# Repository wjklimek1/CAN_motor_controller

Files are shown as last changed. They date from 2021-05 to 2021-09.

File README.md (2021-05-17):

# CAN motor controller
This project is a device that allows control of DC motor by commands on CAN bus. It is based on STM32F103 microcontroller that interprets CAN messages and drives motor using two BTN8982 half-bridges configured as a single H-bridge. 

## Motor driving capabilities
DC motor is controlled with 21kHz PWM signal with 0-100% duty. PWM can be regulated in 0.1% steps - from 0 to 1000. Theoretically max current that MOSFETs can handle is 55A, but it can be futher limited by traces width and connectors. It was tested up to 10A, but should handle much more without any problems. Power supply voltage range is 5-24V.
| Parameter | Min | Max |
|--|--|--|
| voltage | 5V | 24V |
| motor current |  | 55A (10A tested) |

Motor is accelerated slowly by changing PWM duty. If received command orders to immediately set PWM to 100% from 0%, duty is increased slowly in default 10ms intervals. Therefore spinning motor to top speed will take 10s. This property can be disabled by setting "motor inertia" parameter to 0 (see CAN commands table).

## CAN configuration
CAN bus in STM32F103 runs on 250kb/s by default. It can be set to other, hard coded value in the initialization function. Other supported baudrates are 500kb/s and 1Mb/s. 

## Heartbeat
Device emits "heartbeat" frame every 1s. It is an empty frame with ID = 0x444. Heartbeat can be disabled or it's period can be changed in 1s steps up to 255s.

## CAN message structure
Device utilizes two identifiers - 0x444 for commands and 0x445 for requesting data. This values are hard coded too, but can be changed in *canbus.h* file. DLC of CAN messages is not really important, but it cannot be shorter than expected.
In both commands and data requests first byte of message is code of command or data request. In commands next bytes represent values of command parameters. When data request is received by device, it will respond with frame of the same ID and data request code. Next bytes will contain requested data.

## Commands
Following table shows available commands:
|Command | frame ID | DLC | byte 0 (command code) | byte 1 | byte 2 | byte 3 |
|--|--|--|--|--|--|--|
|Set speed | 0x444 | 4 | 1 | rotation direction (0 or 1) | MSB of speed | LSB of speed|
|Set max temperature internal | 0x444 | 2 | 2 | max internal temperature (uint8_t) in Celcius | - | - |
|Set max temperature external | 0x444 | 2 | 3 | max external temperature (uint8_t) in Celcius | - | - |
|Set max current | 0x444 | 4 | 4 | MSB of max current (mA) | LSB of max current (mA) | - |
|Emergency stop | 0x444 | 1 | 5 | - | - | - |
|Set inertia | 0x444 | 2 | 6 | Inertia (ms delay between changing PWM duty) | - | - |
|Set heartbeat | 0x444 | 2 | 7 | heartbeat interval (0 for disabled) | - | - |

## Data requests
To request data, frame of ID = 0x445 and first byte containing data request code can be sent. Device will respond with similar frame, but containing data in next bytes.
 
Following table shows available data requests:
|Data request | frame ID | DLC | byte 0 (data request code) | byte 1 | byte 2 | byte 3 | byte 4 |byte 5 |
|--|--|--|--|--|--|--|--|--|
|Internal temperature | 0x445 | 2 | 1 | Internal temperature (uint8_t) in |Celcius | - | - | - | - |
|External temperature | 0x445 | 2 | 2 | External temperature (uint8_t) in |Celcius | - | - | - | - |
|Power supply voltage | 0x445 | 3 | 3 | MSB of voltage in mV | LSB of voltage in mV | - | - | - |
|Motor current | 0x445 | 3 | 4 | MSB of current in mA | LSB of current in mA | - | - | - |
|Speed | 0x445 | 4 | 5 | rotation direction (0 or 1) | MSB of speed | LSB of speed| - | - |
|Target speed | 0x445 | 4 | 6 | rotation direction (0 or 1) | MSB of speed | LSB of speed| - | - |
|Errors | 0x445 | 5 | 7 | MOSFET fault | overcurrent | overtemperature internal | overtemperature external | emergency stop |

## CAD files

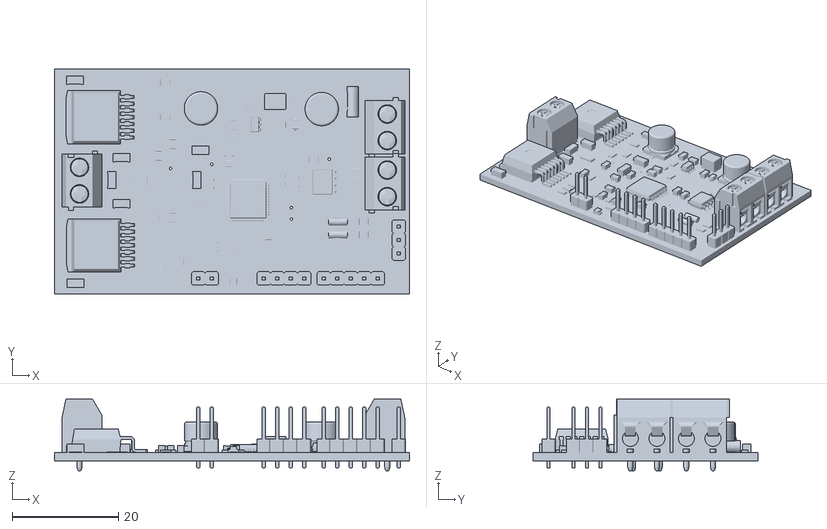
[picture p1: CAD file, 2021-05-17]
PCB_and_schematic/3D_models/CAN_motor_controller.stl
66.8 x 42.4 x 13.5

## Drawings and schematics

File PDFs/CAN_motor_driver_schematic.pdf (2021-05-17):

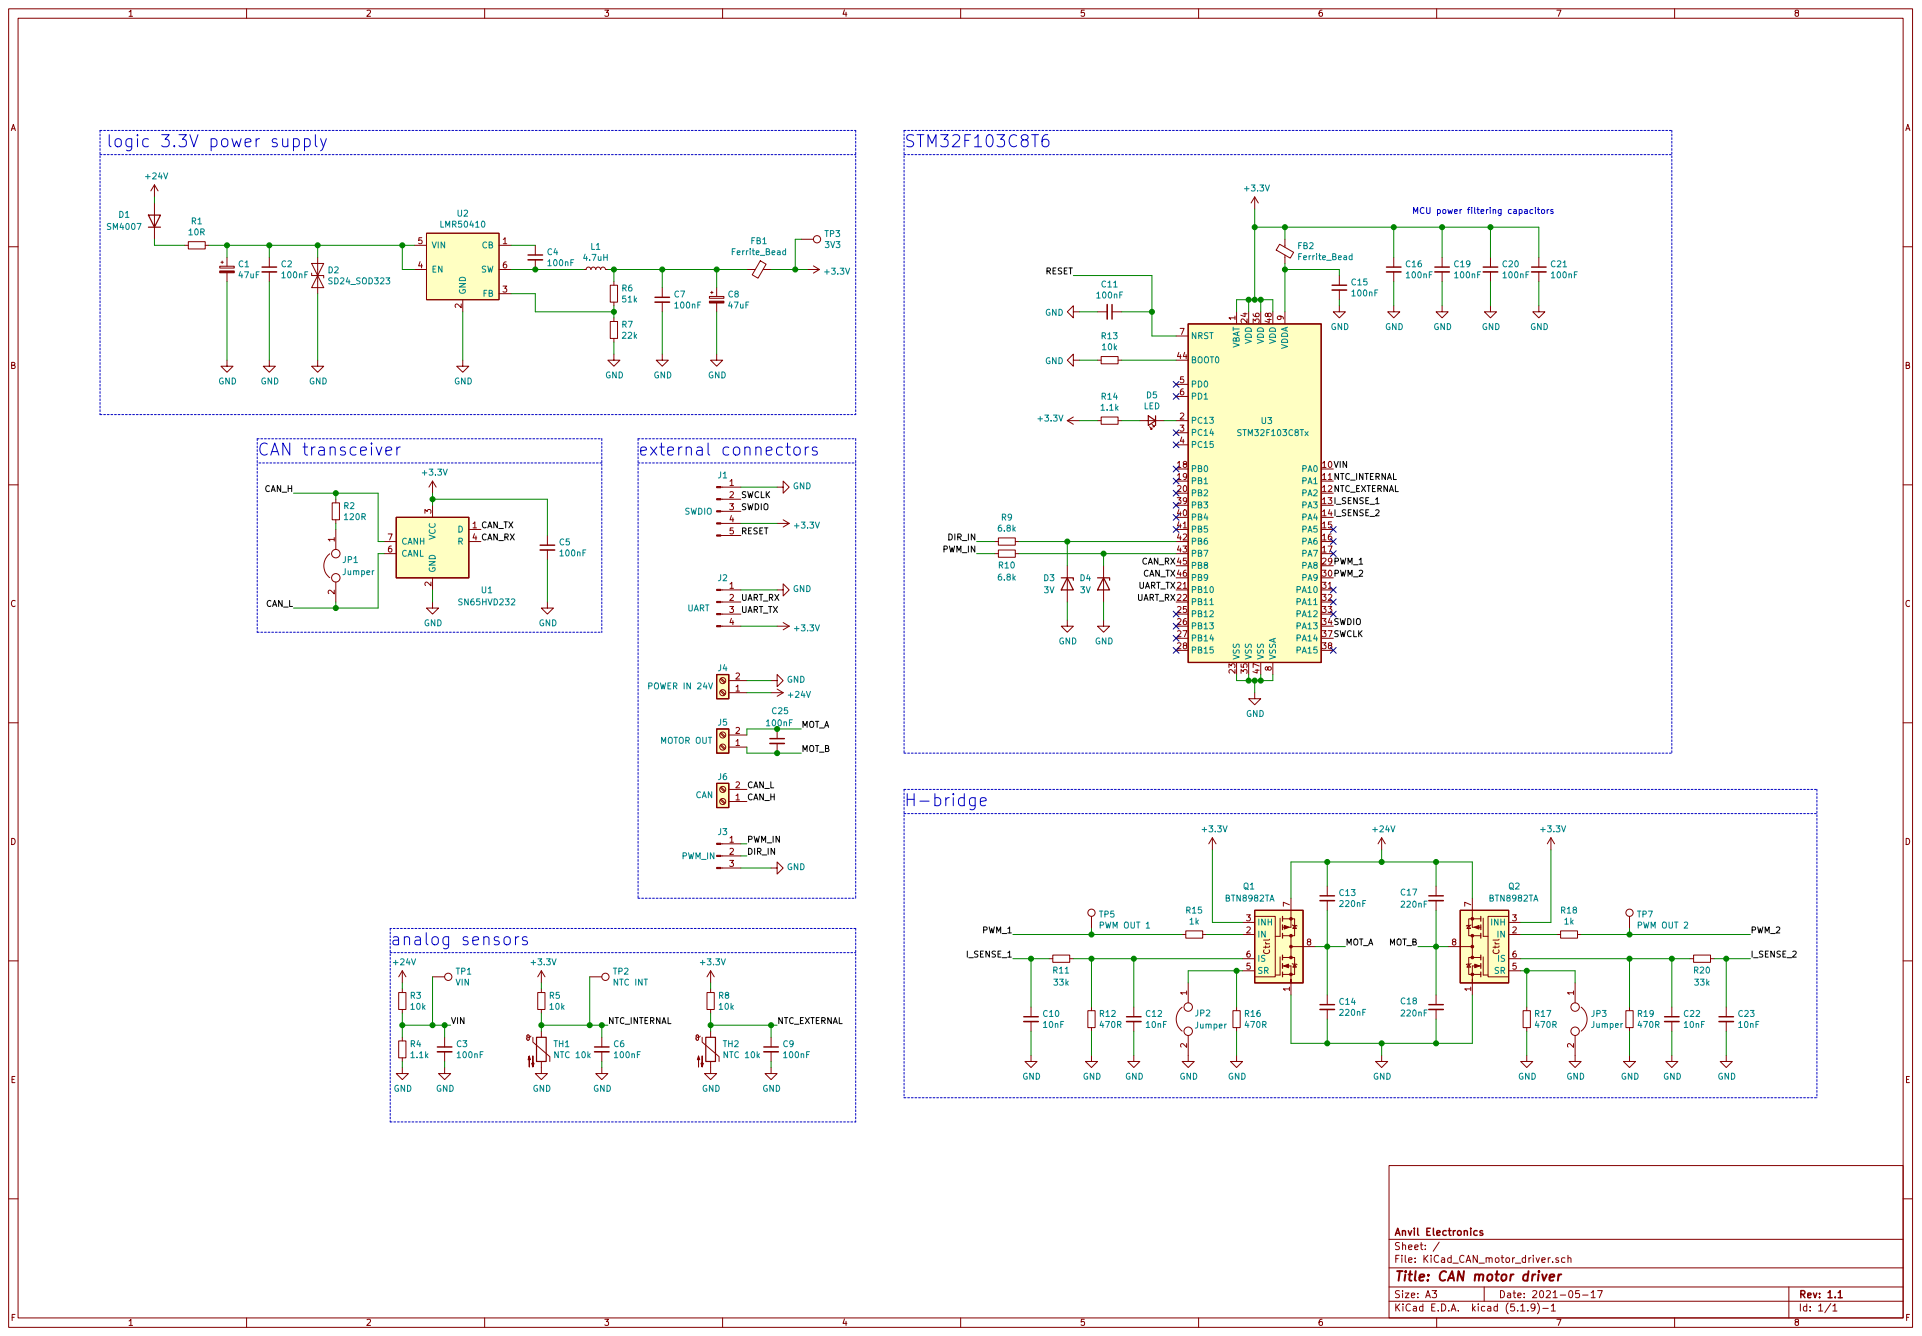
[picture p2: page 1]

2 FB 3 EN 4 VIN 5 SW 6 U2

MCU power filtering capacitors

1 VDD 24 VDD 36 VDD 48 VDDA

9 VSS 23 VSS 35 VSS 47 VSSA

TP7 PWM OUT 2 TP2 NTC INT

File: KiCad_CAN_motor_driver.sch Sheet: / Anvil Electronics

Id: 1/1 Title: CAN motor driver

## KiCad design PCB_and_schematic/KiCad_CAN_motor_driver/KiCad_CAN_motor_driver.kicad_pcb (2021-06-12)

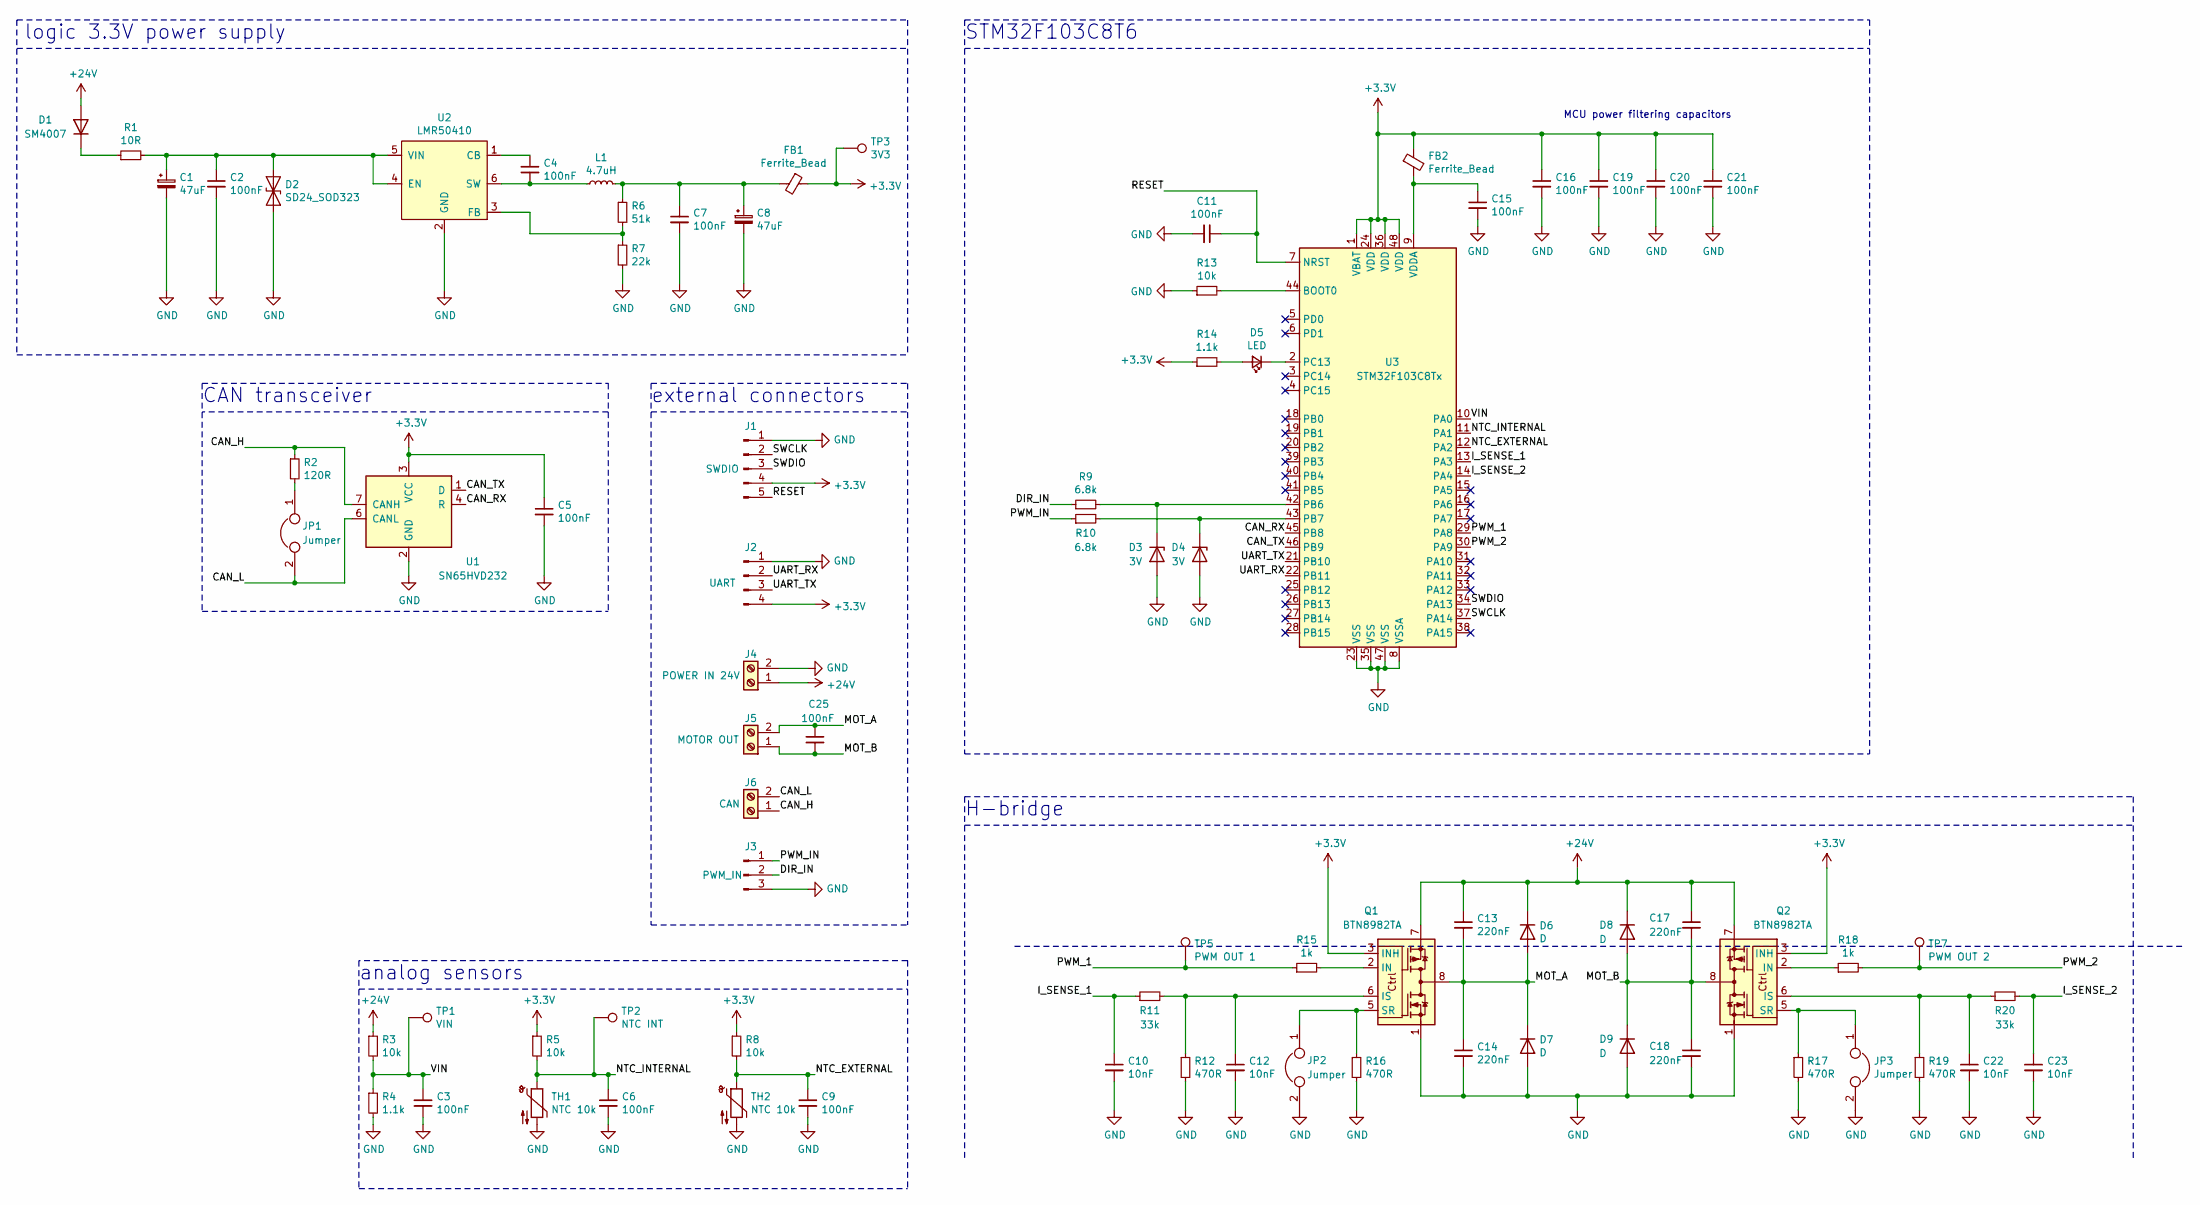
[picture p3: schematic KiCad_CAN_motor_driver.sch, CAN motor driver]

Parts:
C1, C8: 47uF; CP_Elec_6.3x5.7
C2, C3, C4, C5, C6, C7, C9, C11, C15, C16, C19, C20, C21: 100nF; C_0805_2012Metric
C10, C12, C22, C23: 10nF; C_0805_2012Metric
C13, C14, C17, C18: 220nF; C_1206_3216Metric_Pad1.33x1.80mm_HandSolder
C25: 100nF; C_1206_3216Metric
D1: SM4007; D_MELF
D2: SD24_SOD323; D_SOD-323
D3, D4: 3V; D_MiniMELF
D5: LED; LED_0805_2012Metric_Castellated
D6, D7, D8, D9: D; D_PowerDI-123
FB1: Ferrite_Bead; L_1206_3216Metric
FB2: Ferrite_Bead; L_1206_3216Metric_Pad1.22x1.90mm_HandSolder
J1: SWDIO; PinHeader_1x05_P2.54mm_Vertical
J2: UART; PinHeader_1x04_P2.54mm_Vertical
J3: PWM_IN; PinHeader_1x03_P2.54mm_Vertical
J4: POWER IN 24V; ScrewTerminal_2_P5.08mm
J5: MOTOR OUT; ScrewTerminal_2_P5.08mm
J6: CAN; ScrewTerminal_2_P5.08mm
JP1: Jumper; SolderJumper-2_P1.3mm_Open_Pad1.0x1.5mm
JP2, JP3: Jumper; SolderJumper-2_P1.3mm_Bridged_Pad1.0x1.5mm
L1: 4.7uH; L_Wuerth_MAPI-4030
Q1, Q2: BTN8982TA; TO-263-7_TabPin8
R1: 10R; R_0805_2012Metric
R2: 120R; R_0805_2012Metric
R3, R5, R8, R13: 10k; R_0805_2012Metric
R4, R14: 1.1k; R_0805_2012Metric
R6: 51k; R_0805_2012Metric
R7: 22k; R_0805_2012Metric
R9, R10: 6.8k; R_0805_2012Metric
R11, R20: 33k; R_0805_2012Metric
R12, R16, R17, R19: 470R; R_0805_2012Metric
R15, R18: 1k; R_0805_2012Metric
TH1: NTC 10k; R_1206_3216Metric_Pad1.30x1.75mm_HandSolder
TH2: NTC 10k; PinHeader_1x02_P2.54mm_Vertical
TP1: VIN; TestPoint_THTPad_D1.0mm_Drill0.5mm
TP2: NTC INT; TestPoint_THTPad_D1.0mm_Drill0.5mm
TP3: 3V3; TestPoint_THTPad_D1.0mm_Drill0.5mm
TP5: PWM OUT 1; TestPoint_THTPad_D1.0mm_Drill0.5mm
TP7: PWM OUT 2; TestPoint_THTPad_D1.0mm_Drill0.5mm
U1: SN65HVD232; SOIC-8_3.9x4.9mm_P1.27mm
U2: LMR50410; SOT-23-6_Handsoldering
U3: STM32F103C8Tx; LQFP-48_7x7mm_P0.5mm

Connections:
+3V3: C5.1, C16.1, C19.1, C20.1, C21.1, FB1.1, FB2.1, J1.4, J2.4, Q1.3 (INH), Q2.3 (INH), R5.1, R8.1, R14.1, TP3.1, U1.3 (VCC), U3.1 (VBAT), U3.24 (VDD), U3.36 (VDD), U3.48 (VDD)
+24V: C13.1, C17.1, D1.2 (A), D6.1 (K), D8.1 (K), J4.1, Q1.7, Q2.7, R3.1
/CAN_H: J6.1, R2.1, U1.7 (CANH)
/CAN_L: J6.2, JP1.2, U1.6 (CANL)
/CAN_RX: U1.4 (R), U3.45 (PB8)
/CAN_TX: U1.1 (D), U3.46 (PB9)
/DIR_IN: J3.2, R9.1
/I_SENSE_1: C10.1, R11.1, U3.13 (PA3)
/I_SENSE_2: C23.1, R20.2, U3.14 (PA4)
/MOT_A: C13.2, C14.1, C25.1, D6.2 (A), D7.1 (K), J5.2, Q1.4, Q1.8
/MOT_B: C17.2, C18.1, C25.2, D8.2 (A), D9.1 (K), J5.1, Q2.4, Q2.8
/NTC_EXTERNAL: C9.1, R8.2, TH2.1, U3.12 (PA2)
/NTC_INTERNAL: C6.1, R5.2, TH1.1, TP2.1, U3.11 (PA1)
/PWM_1: R15.1, TP5.1, U3.29 (PA8)
/PWM_2: R18.2, TP7.1, U3.30 (PA9)
/PWM_IN: J3.1, R10.1
/RESET: C11.1, J1.5, U3.7 (NRST)
/SWCLK: J1.2, U3.37 (PA14)
/SWDIO: J1.3, U3.34 (PA13)
/UART_RX: J2.2, U3.22 (PB11)
/UART_TX: J2.3, U3.21 (PB10)
/VIN: C3.1, R3.2, R4.1, TP1.1, U3.10 (PA0)
GND: C1.2, C2.2, C3.2, C5.2, C6.2, C7.2, C8.2, C9.2, C10.2, C11.2, C12.2, C14.2, C15.2, C16.2, C18.2, C19.2, C20.2, C21.2, C22.2, C23.2, D2.2 (A2), D3.2 (A), D4.2 (A), D7.2 (A), D9.2 (A), J1.1, J2.1, J3.3, J4.2, JP2.2, JP3.2, Q1.1, Q2.1, R4.2, R7.2, R12.2, R13.1, R16.2, R17.2, R19.2, TH1.2, TH2.2, U1.2 (GND), U2.2 (GND), U3.8 (VSSA), U3.23 (VSS), U3.35 (VSS), U3.47 (VSS)
unnamed: C1.1, C2.1, D2.1 (A1), R1.2, U2.4 (EN), U2.5 (VIN)
unnamed: C4.1, U2.1 (CB)
unnamed: C4.2, L1.1, U2.6 (SW)
unnamed: C7.1, C8.1, FB1.2, L1.2, R6.1
unnamed: C12.1, Q1.6 (IS), R11.2, R12.1
unnamed: C15.1, FB2.2, U3.9 (VDDA)
unnamed: C22.1, Q2.6 (IS), R19.1, R20.1
unnamed: D1.1 (K), R1.1
unnamed: D3.1 (K), R9.2, U3.42 (PB6)
unnamed: D4.1 (K), R10.2, U3.43 (PB7)
unnamed: D5.1 (K), U3.2 (PC13)
unnamed: D5.2 (A), R14.2
unnamed: JP1.1, R2.2
unnamed: JP2.1, Q1.5 (SR), R16.1
unnamed: JP3.1, Q2.5 (SR), R17.1
unnamed: Q1.2 (IN), R15.2
unnamed: Q2.2 (IN), R18.1
unnamed: R6.2, R7.1, U2.3 (FB)
unnamed: R13.2, U3.44 (BOOT0)

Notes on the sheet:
logic 3.3V power supply
MCU power filtering capacitors
external connectors
CAN transceiver
analog sensors
H-bridge
STM32F103C8T6

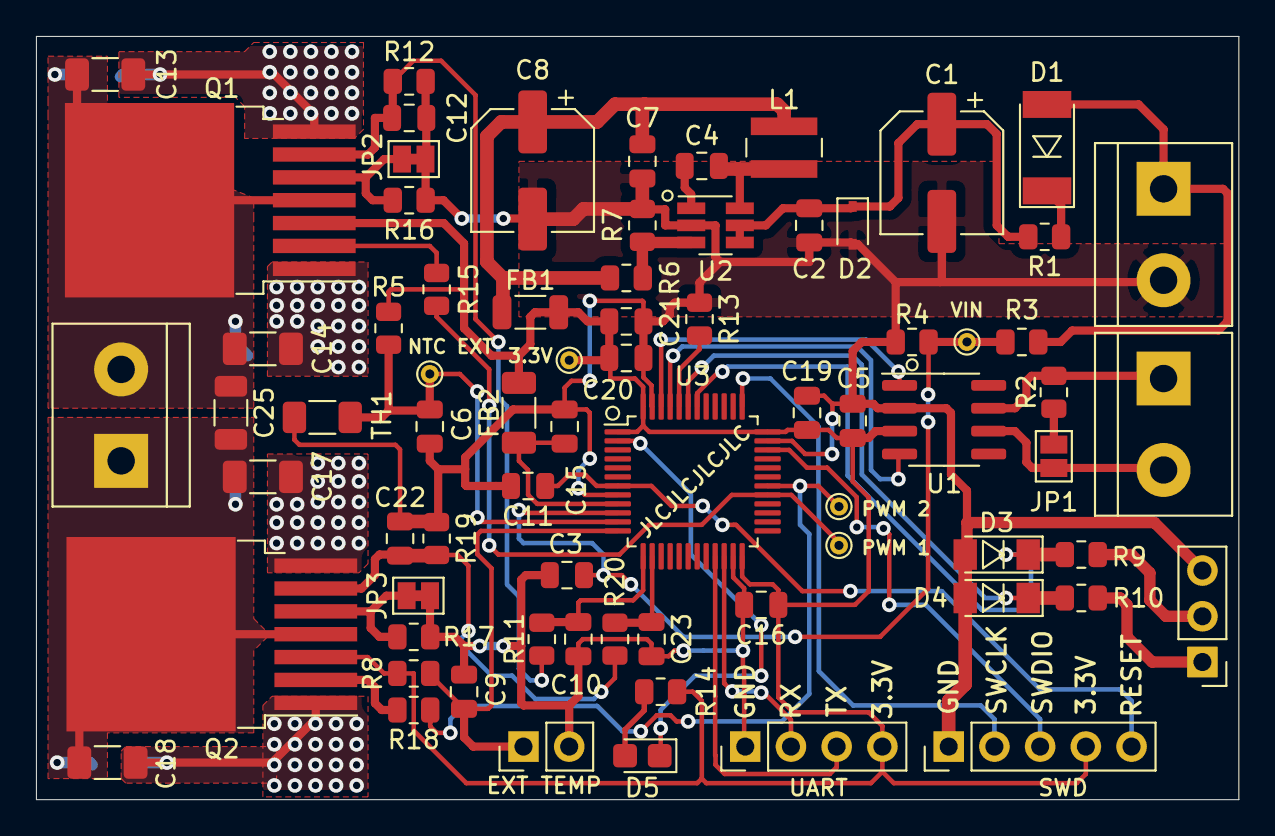
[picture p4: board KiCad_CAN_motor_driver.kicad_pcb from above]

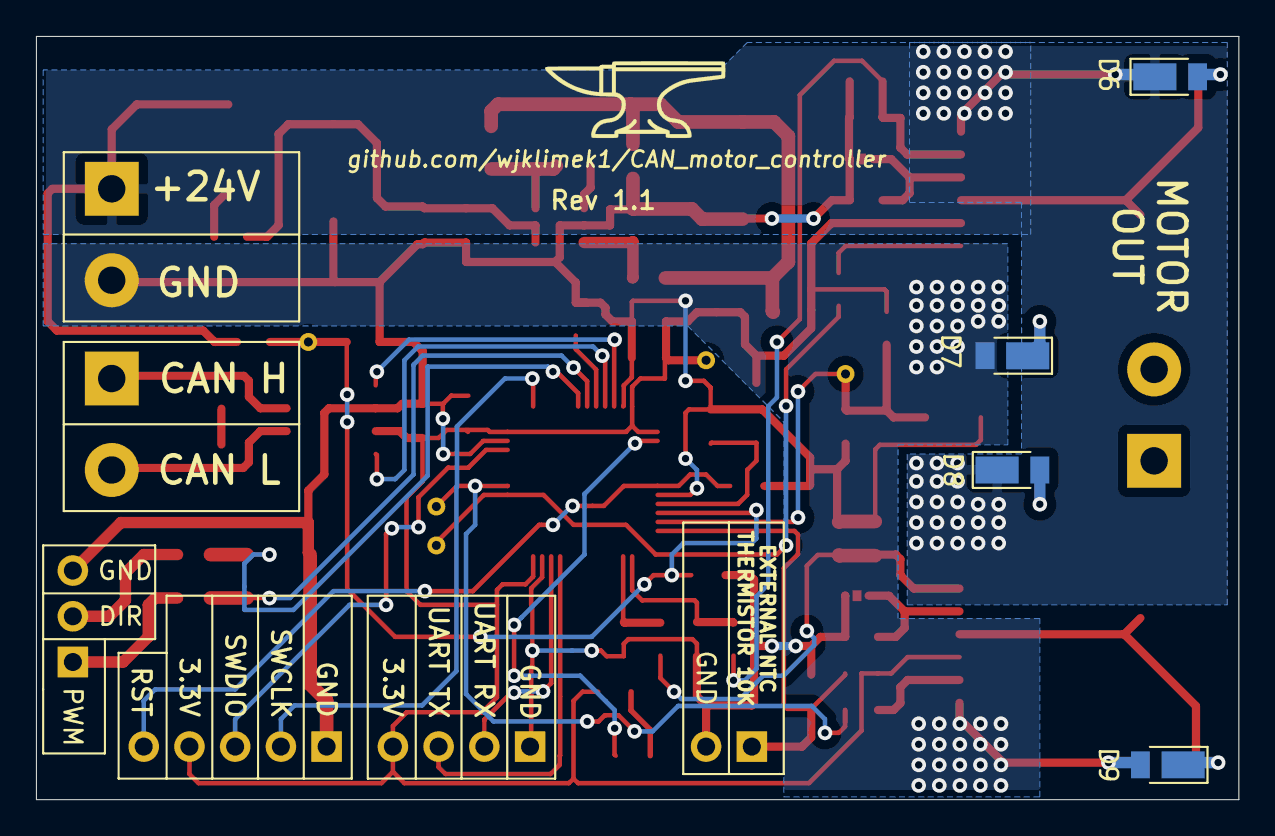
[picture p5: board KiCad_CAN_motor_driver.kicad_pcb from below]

Board: 2 copper layers, 66.8 x 42.4 mm, 77 parts (4 on the bottom side), 42 nets.

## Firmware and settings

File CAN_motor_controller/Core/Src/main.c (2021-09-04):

#include <stdint.h>
#include "stm32f103xb.h"

#include "timers.h"
#include "clock.h"
#include "adc.h"
#include "uart.h"
#include "printf.h"
#include "canbus.h"
#include "ringbuffer.h"
#include "thermistor.h"
#include "command_interpreter.h"

volatile uint16_t ADC_raw_values[6];
volatile CANbus_RX_buffer_t rx_buffer;

int main()
{
  set_system_clock_to_64Mhz();

  SysTick_init(64000);
  TIM1_init_and_start();
  ADC_init();
  ADC_start_with_DMA((uint16_t*)ADC_raw_values);
  UART3_init(64000000, 115200);

  CAN1_init(250000);
  CAN1_config_filter(0, COMMAND_MSG_ID, 0);
  CAN1_config_filter(1, DATARQ_MSG_ID, 1);

  ringbuffer_init(&rx_buffer);

  RCC->APB2ENR |= RCC_APB2ENR_IOPCEN;  //enable gpio port C clock
  GPIOC->CRH &= ~(GPIO_CRH_MODE13_Msk);
  GPIOC->CRH |= (GPIO_CRH_MODE13_1);
  GPIOC->CRH &= ~(GPIO_CRH_CNF13_Msk); //turn on LED

  while(1)
  {
    command_interpreter(&rx_buffer);
    follow_target_speed();
    transmit_heartbeat();
  }
}

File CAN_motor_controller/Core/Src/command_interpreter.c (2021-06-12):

#include <stdint.h>
#include "stm32f103xb.h"

#include "timers.h"
#include "clock.h"
#include "adc.h"
#include "uart.h"
#include "printf.h"
#include "canbus.h"
#include "thermistor.h"
#include "ringbuffer.h"
#include "command_interpreter.h"

extern volatile uint16_t ADC_raw_values[6];
extern volatile CANbus_RX_buffer_t rx_buffer;

uint8_t _heartbeat_interval = 1;
uint8_t _motor_inertia = 10;
uint8_t _emergency_stop = 0;
uint8_t _motor_dir = 0;
uint16_t _motor_speed = 0;
uint8_t _target_motor_dir = 0;
uint16_t _target_motor_speed = 0;

uint8_t _max_current = 30;
uint8_t _max_temperature_int = 90;
uint8_t _max_temperature_ext = 90;

int8_t command_interpreter(volatile CANbus_RX_buffer_t *rx_buffer)
{
  if (ringbuffer_elements_pending(rx_buffer) > 0)
  {
    CANbus_msg_t msg = ringbuffer_get_msg(rx_buffer);

    if (msg.stdID == COMMAND_MSG_ID)
    {
      switch (msg.data[0])
	{
	case SET_SPEED:
	  set_speed(msg);
	  break;
	case SET_MAX_CURR:
	  set_max_curr(msg);
	  break;
	case SET_MAX_TEMP_INTERNAL:
	  set_max_temp_int(msg);
	  break;
	case SET_MAX_TEMP_EXTERNAL:
	  set_max_temp_ext(msg);
	  break;
	case EMERGENCY_STOP:
	  emergency_stop();
	  break;
	case SET_INERTIA:
	  set_motor_inertia(msg);
	  break;
	case SET_HEARTBEAT:
	  set_heartbeat(msg);
	  break;
	default:
	  return UNKNOWN_COMMAND;
	  break;
	}
    }
    else if (msg.stdID == DATARQ_MSG_ID)
    {
      switch (msg.data[0])
	{
	case GET_TEMP_INTERNAL:
	  transmit_temperature_internal();
	  break;
	case GET_TEMP_EXTERNAL:
	  transmit_temperature_external();
	  break;
	case GET_VOLTAGE:
	  transmit_voltage();
	  break;
	case GET_CURRENT:
	  transmit_current();
	  break;
	case GET_SPEED:
	  transmit_motor_speed();
	  break;
	case GET_TARGET_SPEED:
	  transmit_target_motor_speed();
	  break;
	case GET_ERRORS:
	  transmit_errors();
	  break;
	default:
	  return UNKNOWN_DATARQ;
	  break;
	}
    }
    else
    {
      return UNKNOWN_MSG_ID;
    }
  }
  else
    return BUFFER_EMPTY;

  return MESSAGE_PROCESSED;
}

void transmit_temperature_internal()
{
  CANbus_msg_t msg;
  msg.stdID = 0x445;
  msg.RTR = 0;
  msg.DLC = 2;

  msg.data[0] = GET_TEMP_INTERNAL;
  msg.data[1] = get_temperature_internal();

  while(CAN1_transmit_message(msg) < 0);
}

void transmit_temperature_external()
{
  CANbus_msg_t msg;
  msg.stdID = 0x445;
  msg.RTR = 0;
  msg.DLC = 2;

  msg.data[0] = GET_TEMP_EXTERNAL;
  msg.data[1] = get_temperature_external();

  while(CAN1_transmit_message(msg) < 0);
}

void transmit_voltage()
{
  CANbus_msg_t msg;
  msg.stdID = 0x445;
  msg.RTR = 0;
  msg.DLC = 3;

  uint16_t voltage = get_voltage();
  msg.data[0] = GET_VOLTAGE;
  msg.data[1] = voltage >> 8;     //MSB of voltage variable
  msg.data[2] = voltage & 0x00FF; //LSB of voltage variable

  while(CAN1_transmit_message(msg) < 0);
}

void transmit_current()
{
  CANbus_msg_t msg;
  msg.stdID = 0x445;
  msg.RTR = 0;
  msg.DLC = 3;

  uint16_t current = get_current();
  msg.data[0] = GET_CURRENT;
  msg.data[1] = current >> 8;     //MSB of current variable
  msg.data[2] = current & 0x00FF; //LSB of current variable

  while(CAN1_transmit_message(msg) < 0);
}

void transmit_motor_speed()
{
  CANbus_msg_t msg;
  msg.stdID = 0x445;
  msg.RTR = 0;
  msg.DLC = 4;

  msg.data[0] = GET_SPEED;
  msg.data[1] = _motor_dir;
  msg.data[2] = _motor_speed >> 8;     //MSB of motor speed variable
  msg.data[3] = _motor_speed & 0x00FF; //LSB of motor speed variable

  while(CAN1_transmit_message(msg) < 0);
}

void transmit_target_motor_speed()
{
  CANbus_msg_t msg;
  msg.stdID = 0x445;
  msg.RTR = 0;
  msg.DLC = 4;

  msg.data[0] = GET_TARGET_SPEED;
  msg.data[1] = _target_motor_dir;
  msg.data[2] = _target_motor_speed >> 8;     //MSB of targetmotor speed variable
  msg.data[3] = _target_motor_speed & 0x00FF; //LSB of motor speed variable

  while(CAN1_transmit_message(msg) < 0);
}

void transmit_errors()
{
  CANbus_msg_t msg;
  msg.stdID = DATARQ_MSG_ID;
  msg.RTR = 0;
  msg.DLC = 6;

  msg.data[0] = GET_ERRORS;
  if (get_mosfet_fault() == 1)
    msg.data[1] = 1;
  else
    msg.data[1] = 0;

  if (get_current() > _max_current)
    msg.data[2] = 1;
  else
    msg.data[2] = 0;

  if (get_temperature_internal() > _max_temperature_ext)
    msg.data[3] = 1;
  else
    msg.data[3] = 0;

  if (get_temperature_external() > _max_temperature_ext)
    msg.data[4] = 1;
  else
    msg.data[4] = 0;

  if (_emergency_stop == 1)
    msg.data[5] = 1;
  else
    msg.data[5] = 0;

  while(CAN1_transmit_message(msg) < 0);
}

uint8_t get_temperature_internal()
{
  uint32_t millivolts = ADC_raw_values[1] * 3300 / 4095;
  uint32_t resistance = (millivolts * 10000) / (3301 - millivolts);
  float temperature = thermistor_getTemperature_steinhart(resistance, 10000, 3455, 25);
  return (uint8_t) temperature;
}

uint8_t get_temperature_external()
{
  uint32_t millivolts = ADC_raw_values[2] * 3300 / 4095;
  uint32_t resistance = (millivolts * 10000) / (3301 - millivolts);
  float temperature = thermistor_getTemperature_steinhart(resistance, 10000, 3455, 25);
  return (uint8_t) temperature;
}

uint16_t get_voltage()
{
  //exact formula: (Vref/MaxADCval)*ADC_reading * (10/1.1) where 10/1.1 is voltage divider constant
  uint32_t millivolts = ADC_raw_values[0] * 3300 / 4095;
  millivolts = millivolts * (10000 + 1100) / 1100;
  return (uint16_t) millivolts;
}

uint8_t get_current()
{
  const float alpha = 0.1;
  float millivolts;
  float Isense;
  static float current = 0;
  static float new_current = 0;

  if (ADC_raw_values[3] >= ADC_raw_values[4])
    millivolts = ADC_raw_values[3] * 3300 / 4095;
  if (ADC_raw_values[3] < ADC_raw_values[4])
    millivolts = ADC_raw_values[4] * 3300 / 4095;

  Isense = (millivolts / 470) - 0.170f;
  new_current = Isense * 9.165f * 1000;

  current = alpha * new_current + (1 - alpha) * current;

  if (current < 0)
    return 0;

  return (uint8_t) (current / 1000);
}

uint8_t get_mosfet_fault()
{
  if (ADC_raw_values[3] > 2700)
    return 1;
  if (ADC_raw_values[4] > 2700)
    return 1;

  return 0;
}

void set_speed(CANbus_msg_t msg)
{
  _emergency_stop = 0;
  _target_motor_dir = msg.data[1];
  _target_motor_speed = msg.data[2] << 8 | msg.data[3];

  if (_target_motor_speed > 1000)
    _target_motor_speed = 1000;

  if (_target_motor_dir > 1)
    _target_motor_dir = 1;
}

void set_max_curr(CANbus_msg_t msg)
{
  _max_current = msg.data[1] << 8 | msg.data[2];
}

void set_max_temp_int(CANbus_msg_t msg)
{
  _max_temperature_int = msg.data[1];
}

void set_max_temp_ext(CANbus_msg_t msg)
{
  _max_temperature_ext = msg.data[1];
}

void set_motor_inertia(CANbus_msg_t msg)
{
  _motor_inertia = msg.data[1];
}

void set_heartbeat(CANbus_msg_t msg)
{
  _heartbeat_interval = msg.data[1];
}
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

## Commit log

2021-03-20 Initial PCB version
    + initial schematic
    + initial PCB design
    [KiCad_CAN_motor_driver.kicad_pcb, KiCad_CAN_motor_driver.sch]
2021-03-21 Power traces optimization
    +power traces optimized for lower resistance
    [KiCad_CAN_motor_driver.kicad_pcb]
2021-03-21 Added 3D models of PCB in .step and .stl formats
    [CAN_motor_controller.stl]
2021-03-22 PDF schematic
    + schematic in PDF format for quick preview
    + changed resistors on PWM inputs from 1K to 6.8K to decrease Zener diodes current
    + little tweaks in PCB traces
    [KiCad_CAN_motor_driver.kicad_pcb, KiCad_CAN_motor_driver.sch]
2021-03-22 Added vias on power traces near input, added testpoints
    [KiCad_CAN_motor_driver.kicad_pcb, KiCad_CAN_motor_driver.sch]
2021-03-22 Added JLC PCB ID placeholder,
    +traces optimization
    [KiCad_CAN_motor_driver.kicad_pcb]
2021-03-23 Final PCB version (rev 1.0)
    + reduced amount of vias
    + increased distance between vias
    + removed vias from half-bridge's bottom and moved them closer to motor output pads
    + changed PWM input connector to goldpin
    + added jumper (default open) connecting terminating resistor to CAN bus
    + updated PDF schematic
    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
    [CAN_motor_controller.stl, KiCad_CAN_motor_driver.kicad_pcb, KiCad_CAN_motor_driver.sch]
2021-04-04 First version of STM32 code (PWM, PLL)
    Initial version of code for STM32F103C8T6
    + function to switch MCU clock source from HSI to 64MHz PLL
    + function to init timer 1 with 2 PWM outputs on pins PA8 and PA9
2021-04-05 ADC + DMA
    + reading analog values from PA0, PA1, PA2, PA3 and internal temperature sensor
    + working ADC+DMA for continous readings without CPU utilization
    + moved clock configuration and timers functions to separate files
2021-04-08 UART with printf() support
    + added UART3 initialization and data send functions
    + added printf() implementation suitable for embedded systems
    + standardized code formatting
2021-04-08 Simple CANbus frame transmission
    + CANbus initialization
    + Transmission of single CAN frame using mailbox0
2021-04-11 Receiving CAN bus messages
    + standarized CAN bus frame structure for transmission and reception
    + functions to check if there are any pending messages in mailboxes
    + function to receive CAN bus message from mailboxes
2021-04-12 Enabled CAN1 reception interrupts
    + CAN1 reception IRQs enabled and ready to be implemented
2021-04-12 Interrupt based CAN reception with ring buffer
    + implemented CAN RX interrupts
    + implemented simple ring buffer to keep incoming CAN messages
    + changed CANbus_msg_t from struct to typedef struct
    + removed file accidendtaly placed in "Startup" folder
2021-04-22 Thermistor and getTick()
    + added function to convert thermistor resistance to temperature
    + added function getTick() returning current value of milliseconds counter
2021-04-22 Enabled CAN ID filters
    + enabled CAN ID filters to allow only commands and data requests IDs
    + fixed bug in function releasing mailbox1
    [canbus.c, main.c]
2021-04-26 Utilizing all TX mailboxes, fixed volatile warning
    + utilizing all 3 TX mailboxes for CAN
    + change return data for CAN1_transmit_message() function
    + fixed "discards volatile quantifier" warnings
    [canbus.c, main.c]
2021-04-26 DMA initialization placed in ADC code, unified UART3_init() with actual core clock
    + DMA initialization placed in ADC code
    + unified UART3_init() with actual core clock
    + Doxygen style comments in ringbuffer files
2021-04-29 Commands setting internal parameters
    + commands for setting global variables: target motor speed, max current, max internal temperature, max external temperature
    + doxygen style commands in canbus.c file
2021-04-30 Changing motor speed with interpolation
    + function triggered in regular intervals that will interpolate motor speed
    + fixed bug in thermistor calculations
    [command_interpreter.c, main.c]
2021-04-30 Fixed motor speed interpolation
    + fixed bugs in motor speed interpolation
    +fixed potential zero-division error in temperature reading
    + fixed wrong calculation of input voltage
    + request for current motor speed now returns also direction
    +
    [command_interpreter.c, main.c]
2021-05-01 curent calculation
    + calculation of motor current
2021-05-01 Emergency stop, heartbeat, motor inertia
    + settable motor inertia
    + emergency stop command - stops motor without interpolation
    + function transmitting heartbeat
2021-05-01 Fixed freezing after emergency stop
    + after emergency stop all motor related variables are set to 0
    [command_interpreter.c]
2021-05-01 Heartbeat interval and reading errors
    + added function reading following errors: overcurrent, overtemperature internal and external, emergency stop, mosfet fault
    + heartbeat can be enabled or disabled
    + settable heartbeat interval 1-255 seconds
    [command_interpreter.c, main.c]
2021-05-17 PCB and schematic rev 1.1
    + revision 1.1 of schematic and PCB
    [CAN_motor_controller.stl, KiCad_CAN_motor_driver.kicad_pcb, KiCad_CAN_motor_driver.sch]
2021-06-12 Added back-emf diodes, fixed reading errors
    [KiCad_CAN_motor_driver.kicad_pcb, KiCad_CAN_motor_driver.sch]
2021-09-04 Separate function for CAN filter config
    + Separate function to configure CAN filters. Gives more flexibility in filter configuration.
    + fixed some spelling errors and misplaced line in schematic
    [KiCad_CAN_motor_driver.sch]
2021-09-04 Completed comments for thermistor.c and uart.c
